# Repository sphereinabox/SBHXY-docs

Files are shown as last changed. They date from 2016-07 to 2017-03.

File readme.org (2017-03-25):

* SBHXY
SBHXY is an open source 3d Printer design using the [[http://corexy.com][Core XY]] motion system for XY, and is made in [[http://reprap.org][RepRap]] style except with a mix of printed and lasercut parts.

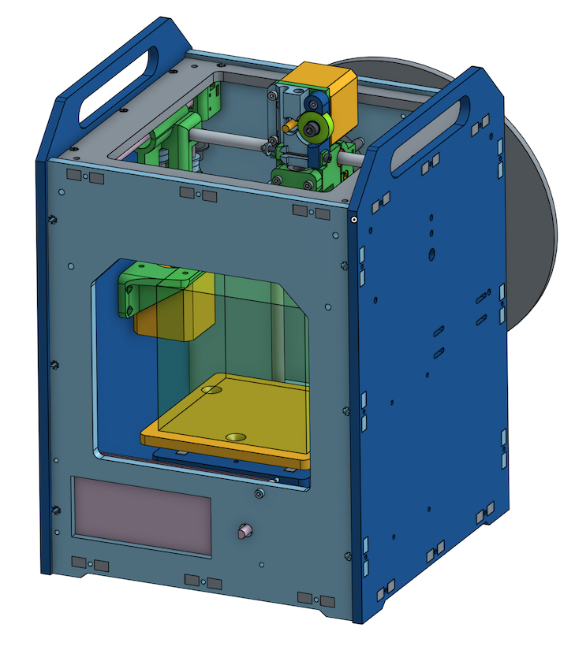
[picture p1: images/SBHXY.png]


SBHXY is licensed GPL v3.

SBHXY was designed to fit a small print volume in a relatively small amount of desk space. The print volume is 100x100x100mm, but the exterior dimensions, without print spool or top wires is only 227x220x316mm.

SBHXY was prototyped at the [[http://sbhackerspace.com][Santa Barbara Hackerspace]].

* TODO:
 - Add section to readme about getting started building this thing before getting to build manual
 - Make licensing + copyright notes in OnShape document
 - Link to OnShape document
 - DXFs are for the black or white Melamine which is 6.7mm thick?
 - Printrboard LCD PCB

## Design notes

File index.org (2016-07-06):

The assembly manual for the SBHXY: [[./build-manual.html]]

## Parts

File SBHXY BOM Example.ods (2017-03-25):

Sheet: BOM by Assembly
Qty | Part | Subassembly | Notes
2 | Printed Top Corner for Idler | Top Belt Idler
10 | M4 Hex Nut | Top Belt Idler
8 | M4x14 SHCS | Top Belt Idler | Only 4 really required. The top plate 2, and the lower printed part 2.
2 | M4x40 SHCS | Top Belt Idler
8 | 624 bearing for belt idler | Top Belt Idler
6 | M4 Flat Washer | Top Belt Idler | Go between pairs of bearings, and between bearings and printed parts
2 | Printed Bottom Corner for Idler | Top Belt Idler
2 | Printed Top Corner for Pulley (has bearing indent) | Top Belt Pulley End
2 | 625 Bearing 5x16x5 | Top Belt Pulley End
1 | Printed pulley spacer (shorter) | Top Belt Pulley End
1 | Printed pulley spacer (longer) | Top Belt Pulley End
2 | GT-2 Pulley 20 teeth 5mm bore | Top Belt Pulley End
2 | 5mm shaft, 100mm long | Top Belt Pulley End
6 | M4 Hex Nut | Top Belt Pulley End
6 | M4x14 SHCS | Top Belt Pulley End | Only top 2 required. Others may misalign rails
2 | 8mm hardened smooth rod, 173mm length | Top Belt Pulley End | Length must be within 1mm for lasercut frame length to fight tightly. Typically Y travel + 50 + 20 + homing margin
1 | Homing Switch SS-5GL | Top Belt Pulley End | S5GL size
2 | #4-1/2" wood screw | Top Belt Pulley End | Screws into printed plastic part
4 | M4 Hex Nut | Back Belt Pulley End
4 | M4x14 SHCS | Back Belt Pulley End
2 | 625 Bearing 5x16x5 | Back Belt Pulley End
2 | GT-2 Pulley 20 teeth 5mm bore | Back Belt Pulley End
2 | Stepper Motor 40mm long | AB Motors
2 | GT-2 Pulley 20 teeth 5mm bore | AB Motors
2.5 | GT-2 Belt length in meters | AB Motors | Should be 1 length over 2300mm long, or two lengths over 1200mm
8 | M3x10 SHCS | AB Motors
8 | M3 Flat Washer | AB Motors
8 | M3x12 SHCS | AB Motors
8 | M3 Flat Washer | AB Motors
8 | M3 Nylon Lock Nut | AB Motors | Hex nuts work but I found they get loose
2 | 140mm GT2 closed loop belt | AB Motors
1 | Printed Left X end | X Ends
1 | Printed Right X end | X Ends
4 | Printed X End Bearing Spacer | X Ends
8 | 624 bearing for belt idler | X Ends
4 | M4x45 SHCS | X Ends
4 | M4 Hex Nut | X Ends
4 | M4 Flat Washer | X Ends | Goes between bearings and printed x-end
2 | LM8LUU Linear Bearing 8x15x45 | X Ends
2 | 8mm hardened smooth rod, 173mm length | X Ends
1 | Printed Extruder Back Half | X Carriage Back Half
4 | LM8SUU Linear Bearing 8x15x17 | X Carriage Back Half
1 | Homing Switch - Small D2F-01L-D3 | X Carriage Back Half | This is smaller than the other homing switches
1 | #4-1/2" Wood screw | X Carriage Back Half
1 | 5015 12V Blower | X Carriage Back Half
2 | M3x20 FHCS | X Carriage Back Half | Phillips or hex is your choice . M3x20 SHCS may work but may rub in back of machine.
4 | M3 Hex Nut | X Carriage Back Half | Nut trap for blower duct, and blower
3 | M3 Hex Nut | X Carriage Back Half | Nut Traps for front half
2 | M3x35 SHCS | X Carriage Back Half | Belt tension adjustment screws
2 | M3 Hex Nut | X Carriage Adjustable Belt Clamp
1 | Printed Extruder Belt Clamp | X Carriage Adjustable Belt Clamp | The belt presses into a slot
1 | Printed Extruder Belt Clamp Mirror | X Carriage Adjustable Belt Clamp
2 | M3x35 SHCS | X Carriage Adjustable Belt Clamp
1 | Printed X Fixed belt clamp (ribbed plate with single hole) | X Carriage Fixed Belt Clamp
1 | M3x16 SHCS | X Carriage Fixed Belt Clamp
1 | Printed X carriage front half | X Carriage Front Half
3 | M3x25 SHCS | X Carriage Front Half | These hold front/back together
2 | M3 Hex Nut | X Carriage Front Half | Nut trap for hotend clamp
1 | Stepper Motor 40mm long | X Carriage Front Half | Extruder motor
1 | M3x10 FHCS | X Carriage Front Half | Phillips or socket is your choice. The material is not thick enough for a standard socket head screw
1 | Filament Drive Gear (6mm hobb diameter) | X Carriage Front Half
3 | 4 inch nylon zip tie | X Carriage Front Half | Mount to linear bearings
1 | Printed Hotend Clamp | X Carriage Front Half | Hold thermistor in place
2 | M3 Hex Nut | X Carriage Front Half | Nut trap for hotend clamp
1 | Printed Extruder Blower Duct | X Carriage Duct
2 | M3x10 SHCS | X Carriage Duct
1 | Printed Hotend Clamp | Hotend Clamp
2 | M3x20 SHCS | Hotend Clamp
1 | Printed Extruder Plate | Extruder Plate
2 | M3x12 SHCS | Extruder Plate
2 | 4 inch nylon zip tie | Extruder Plate
1 | Large filament Guide Tube (approx 1/4" OD) maybe 18" long max | Extruder Plate
1 | Printed Extruder Idler Lever Arm | Extruder Lever Arm
1 | M3x16 SHCS | Extruder Lever Arm | Pivot
1 | 608 Bearing | Extruder Lever Arm | Filament idler bearing
1 | M5x10 SHCS | Extruder Lever Arm | Screws into printed part, holds idler bearing in place
1 | M5 Flat Washer | Extruder Lever Arm
1 | M3x45 SHCS | Extruder Tension Adjustment Bolt
2 | Printed Extruder Idler Pivot | Extruder Tension Adjustment Bolt
2 | M4 Flat Washer | Extruder Tension Adjustment Bolt | Large enough to keep spring on bolt
1 | Extruder Spring | Extruder Tension Adjustment Bolt
1 | M3 Hex Nut | Extruder Tension Adjustment Bolt
1 | E3d V6 Lite | Hotend Assembly | Includes thermistor, heater cartridge, 30mm fan, duct for fins, and PTFE tubing sticking out about 3 inches of groove mount.
1 | Printed Z Idler | Z Top Rod Holder
2 | M3 Hex Nut | Z Top Rod Holder
2 | M3x12 SHCS | Z Top Rod Holder | Through back plane
2 | 624 bearing for belt idler | Z Top Rod Holder
2 | M4 Flat Washer | Z Top Rod Holder
1 | M4 Hex Nut | Z Top Rod Holder
1 | M4x20 SHCS | Z Top Rod Holder
1 | Printed Z motor Mount | Z Bottom Rod Holder
2 | 8mm hardened smooth rod, 173mm length | Z Bottom Rod Holder
1 | Stepper Motor 40mm long | Z Bottom Rod Holder
4 | M3x10 SHCS | Z Bottom Rod Holder
1 | GT-2 Pulley 20 teeth 5mm bore | Z Bottom Rod Holder
6 | M3 Hex Nut | Z Bottom Rod Holder
6 | M3x12 SHCS | Z Bottom Rod Holder | 4 through bottom, 2 through back of frame
1 | Printed Z homing switch mount | Z Homing Switch Mount
1 | Homing Switch SS-5GL | Z Homing Switch Mount
2 | #4-1/2" Wood Screw | Z Homing Switch Mount
2 | M3 Hex Nut | Z Homing Switch Mount
2 | M3x25 SHCS | Z Homing Switch Mount
1 | Lasercut Z Carriage Back | Z Carriage
2 | Lasercut Z Carriage Side | Z Carriage
1 | Lasercut Z Carriage Top | Z Carriage | This has slots to fit into the side pieces
1 | Lasercut Print Bed | Z Carriage | This has 3 holes. They need to be drilled countersunk
4 | Printed Z Bearing Holder | Z Carriage
1 | Printed Z Belt Holder | Z Carriage
2 | LM8LUU Linear Bearing 8x15x45 | Z Carriage | 4 of LM8UU is fine
8 | M3 Hex Nut | Z Carriage | Inside nut traps on printed parts
6 | M3x12 SHCS | Z Carriage | Go into printed parts
2 | M3x16 SHCS | Z Carriage | Z Homging Switch Adjustment mount
3 | M3x30 FHCS | Z Carriage | Bed-level adjustment
4 | M3 Hex Nut | Z Carriage | Captive in side lasercut pieces
4 | M3x12 SHCS | Z Carriage | Through Z top plate into side lasercut pieces
3 | Extruder Spring | Z Carriage | Bed-level adjustment
3 | Printed Thumb Nut Adapter | Z Carriage | Bed-level adjustment
6 | M3 Hex Nut | Z Carriage | Bed level adjustment, and holding bed screws in place
1 | Painters Tape, approx 5 inches square | Z Carriage | Print surface
0.4 | GT-2 Belt length in meters | Z Carriage
1 | Printed Z Homing Switch Adjust | Z Carriage Homing Adjust
1 | M3x20 SHCS | Z Carriage Homing Adjust
1 | Extruder Spring | Z Carriage Homing Adjust
1 | M3 Hex Nut | Z Carriage Homing Adjust
2 | M4 Flat Washer | Z Carriage Homing Adjust
1 | Lasercut top plate | Top Plate
12 | M3 Hex Nut | Top Plate | Nut Traps
1 | Lasercut back plate | Back Plate
6 | M3 Hex Nut | Back Plate | Nut Traps
6 | M3x12 SHCS | Back Plate | Into other panel nut traps
1 | Printed Spool Holder | Back Plate
1 | Printed Power Jack Mount | Power Jack Mount
1 | Panel Mount Barrel Jack Cable | Power Jack Mount
2 | M3 Hex Nut | Power Jack Mount
2 | M3x12 SHCS | Power Jack Mount
1 | Printed Filament Guide Mount | Filament Guide Mount
2 | 4 inch nylon zip tie | Filament Guide Mount
2 | M3 Hex Nut | Filament Guide Mount
2 | M3x12 SHCS | Filament Guide Mount
1 | Lasercut Left Plate | Left Plate
12 | M3x12 SHCS | Left Plate | Into other panel nut traps
1 | Lasercut Right Plate | Right Plate
12 | M3x12 SHCS | Right Plate | Into other panel nut traps
1 | Printrboard electronics | Right Plate
4 | Electronics Spacers 2mm tall | Right Plate | Printrboard mounting
4 | M3 Nylon Lock Nut | Right Plate | Printrboard mounting
4 | M3x20 SHCS | Right Plate | Printrboard mounting
1 | Lasercut Bottom Plate | Bottom Plate | Into ends of extrusion
12 | M3 Hex Nut | Bottom Plate | Nut Traps
4 | Adhesive rubber foot | Bottom Plate | Must be over 8mm tall. The foot should be adhesive to the bottom plate not to the thin laser edge
1 | Lasercut Front Plate | Front Plate
6 | M3 Hex Nut | Front Plate | Nut Traps
6 | M3x12 SHCS | Front Plate | Into other panel nut traps
1 | RepRapDiscount Smart Controller (20x4 Text) | Front Plate | LCD Mounting
4 | M3 Nylon Lock Nut | Front Plate | LCD Mounting
4 | Printed LCD Spacer (10mm) | Front Plate | LCD Mounting
1 | Printed LCD Knob | Front Plate
4 | M3x25 SHCS | Front Plate | LCD Mounting
6 | M3 Hex Nut | Front Plate | Nut Traps
1 | Printrboard LCD+fans PCB | Printrboard add-on
2 | [mosfet] | Printrboard add-on
2 | [diode] | Printrboard add-on
? | [connectors?] | Printrboard add-on
1 | Allen Key Set | Tools
1 | Spool of PLA filament, 1.75mm diameter | Tools
1 | USB A to Micro B cable | Tools
1 | 12V 6A power supply | Electronics

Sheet: BOM by Part
Part Name | Qty Required | Source | Price | Qty | Notes
Lasercut Top Plate | 1
Lasercut Bottom Plate | 1
Lasercut Back Plate | 1
Lasercut Front Plate | 1
Lasercut Left Plate | 1
Lasercut Right Plate | 1
Lasercut Z Carriage Back | 1
Lasercut Z Carriage Side | 2
Lasercut Z Carriage Top | 1
Lasercut Print Bed | 1
Printed Top Corner for Idler | 2
Printed Bottom Corner for Idler | 2
Printed Top Corner for Pulley (has bearing indent) | 2
Printed pulley spacer (shorter) | 1
Printed pulley spacer (longer) | 1
Printed Left X end | 1
Printed Right X end | 1
Printed X End Bearing Spacer | 1
Printed Extruder Back Half | 1
Printed Extruder Belt Clamp | 1
Printed Extruder Belt Clamp Mirror | 1
Printed X Fixed belt clamp (ribbed plate with single hole) | 1
Printed X carriage front half | 1
Printed Hotend Clamp | 2
Printed Extruder Blower Duct | 1
Printed Extruder Plate | 1
Printed Extruder Idler Lever Arm | 1
Printed Extruder Idler Pivot | 2
Printed Z Idler | 1
Printed Z motor Mount | 1
Printed Z homing switch mount | 1
Printed Z Bearing Holder | 4
Printed Z Belt Holder | 1
Printed Thumb Nut Adapter | 3
Printed Z Homing Switch Adjust | 1
Printed Power Jack Mount | 1
Printed Filament Guide Mount | 1
Printed Spool Holder | 1
Printed LCD Spacer (10mm) | 4
Printed LCD Knob | 1
Filament Drive Gear (6mm hobb diameter) | 1 | http://www.robotdigg.com/product/242/MK8-Filament-Drive-Gear | $3.00 | 1
Homing Switch SS-5GL | 2 | http://www.robotdigg.com/product/141/Endstop,-Snap-Action-Limit-Switch-SS-5GL | $0.60 | 1 | No wires
Homing Switch - Small D2F-01L-D3 | 1 | http://www.digikey.com/product-detail/en/D2F01LD3/Z5203-ND/1811799 | $20.50 | 10 | -D3 is for soldering leads on. Without extension is intended for PCB and is .25 to .50 cheaper
Stepper Motor 40mm long | 4 | http://www.robotdigg.com/product/7/NEMA17-Stepper-Motor-40mm-Long,-1.2A | $6.80 | 1
608 Bearing | 1 | http://www.robotdigg.com/product/12/608ZZ-Ball-Bearing | $0.30 | 1
625 Bearing 5x16x5 | 4 | http://www.robotdigg.com/product/63/625ZZ+Ball+Bearing | $4.00 | 10
GT-2 Belt length in meters | 2.9 | http://www.robotdigg.com/product/10/Open-Ended-6mm-Width-GT2-Belt | $1.80 | 1 | Sold by meter
140mm GT2 closed loop belt | 2 | http://www.robotdigg.com/product/88/140mm,+150mm+OR+154mm+2GT-6+endless+belt | $0.35 | 1
LM8LUU Linear Bearing 8x15x45 | 4 | http://www.robotdigg.com/product/302/LM8LUU+8*15*45+Linear+Bearing | $1.00 | 1
LM8SUU Linear Bearing 8x15x17 | 4 | http://www.robotdigg.com/product/477/LMS8UU+Short+Linear+Bearing | $0.60 | 1
GT-2 Pulley 20 teeth 5mm bore | 7 | http://www.robotdigg.com/product/9/GT2-Pulley-20-Teeth-5mm-Bore | $1.80 | 1
5015 12V Blower | 1 | http://www.robotdigg.com/product/194/5015+12V+Blow+Fan | $1.40 | 1 | 0.1A version
E3d V6 Lite | 1 | http://www.filastruder.com/products/lite6 | $35.00 | 1 | 1.75mm 12V Direct version still comes with enough bowden tube
Printrboard electronics | 1
Printrboard to barrel jack adapter cable | 0
12V 6A power supply | 1
RepRapDiscount Smart Controller (20x4 Text) | 1 | http://www.robotdigg.com/product/122/RAMPS+LCD2004+with+SD+Socket | $10.80 | 1 | Poor assembly quality and encoder
8mm hardened smooth rod, 173mm length | 6 | Misumi PSFJ8-173 | $6.70 | 1 | Hard chromed
5mm shaft, 100mm long | 2 | http://www.amazon.com/Helicopter-100mm-Ground-Shaft-Round/dp/B00NQ9NBWQ/ | $9.00 | 10
Extruder Spring | 5 | http://www.mcmaster.com/nav/enter.asp?partnum=9657K274 | $9.80 | 12
Allen Key Set | 1 | http://www.robotdigg.com/product/128/1.5,-2,-2.5,-3,-4-size-allen-key-with-ball-head-in-pack | $2.00 | 1
4 inch nylon zip tie | 7 | http://www.robotdigg.com/product/127/Nylon-Cable-Ties-2.5*100mm-100pcs-n-3.6*200mm-100pcs-Pack | $1.80 | 100 | Probably should specify 2.5 or 3.6mm width when ordering
USB A to Micro B cable | 1 | http://www.monoprice.com/Product?c_id=103&cp_id=10303&cs_id=1030307&p_id=4867&seq=1&format=2 | $0.74 | 1
Spool of PLA filament, 1.75mm diameter | 1 |  | $30.00 | 1
M2.5x5 SHCS | 0 | https://www.boltdepot.com/Product-Details.aspx?product=6369 | $6.13 | 100
M2.5x6 SHCS | 0 | https://www.boltdepot.com/Product-Details.aspx?product=6370 | $6.44 | 100
M2.5x8 SHCS | 0 | https://www.boltdepot.com/Product-Details.aspx?product=6371 | $6.50 | 100
M2.5x10 SHCS | 0 | https://www.boltdepot.com/Product-Details.aspx?product=6372 | $7.28 | 100
M2.5x12 SHCS | 0 | https://www.boltdepot.com/Product-Details.aspx?product=6373 | $9.09 | 100
M2.5x16 SHCS | 0 | https://www.boltdepot.com/Product-Details.aspx?product=6374 | $10.53 | 100
M2.5x20 SHCS | 0 | https://www.boltdepot.com/Product-Details.aspx?product=6375 | $11.70 | 100
M2.5 Flat Washer | 0 | https://www.boltdepot.com/Product-Details.aspx?Units=Metric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 | $1.05 | 100
M2.5 Hext Nut | 0 | https://www.boltdepot.com/Product-Details.aspx?Units=Metric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 | $1.75 | 100
M3x8 SHCS | 0 | https://www.boltdepot.com/Product-Details.aspx?product=6379 | $3.60 | 100
M3x10 SHCS | 14 | https://www.boltdepot.com/Product-Details.aspx?product=6380 | $3.78 | 100
M3x12 SHCS | 68 | https://www.boltdepot.com/Product-Details.aspx?product=6381 | $3.92 | 100
M3x16 SHCS | 4 | https://www.boltdepot.com/Product-Details.aspx?product=6382 | $3.97 | 100
M3x20 SHCS | 7 | https://www.boltdepot.com/Product-Details.aspx?product=6383 | $4.28 | 100
M3x25 SHCS | 9 | https://www.boltdepot.com/Product-Details.aspx?product=6384 | $5.16 | 100
M3x30 SHCS | 0 | https://www.boltdepot.com/Product-Details.aspx?product=6385 | $6.09 | 100
M3x35 SHCS | 4 | https://www.boltdepot.com/Product-Details.aspx?product=6386 | $9.29 | 100
M3x40 SHCS | 0 | https://www.boltdepot.com/Product-Details.aspx?product=6387 | $9.73 | 100
M3x45 SHCS | 1 | https://www.boltdepot.com/Product-Details.aspx?product=6388 | $10.84 | 100
M3x20 Flat Head | 0 | https://www.boltdepot.com/Product-Details.aspx?product=6869 | $5.55 | 100
M3x25 Flat Head | 0 | https://www.boltdepot.com/Product-Details.aspx?product=6870 | $7.10 | 100
M3 Flat Washer | 16 | https://www.boltdepot.com/Product-Details.aspx?product=4513 | $1.10 | 100
M3 Hex Nut | 89 | https://www.boltdepot.com/Product-Details.aspx?product=4773 | $1.80 | 100
M3 Nylon Lock Nut | 16 | https://www.boltdepot.com/Product-Details.aspx?product=4792 | $3.19 | 100
M3 Lock Washer | 0 | https://www.boltdepot.com/Product-Details.aspx?product=14836 | $1.90 | 100
M4x10 SHCS | 0 | https://www.boltdepot.com/Product-Details.aspx?product=6393 | $4.92 | 100
M4x12 SHCS | 0 | https://www.boltdepot.com/Product-Details.aspx?product=6394 | $5.42 | 100
M4x14 SHCS | 18 | https://www.boltdepot.com/Product-Details.aspx?product=6395 | $5.78 | 100
M4x16 SHCS | 0 | https://www.boltdepot.com/Product-Details.aspx?product=6396 | $6.01 | 100
M4x18 SHCS | 0 | https://www.boltdepot.com/Product-Details.aspx?product=6397 | $8.66 | 100
M4x20 SHCS | 1 | https://www.boltdepot.com/Product-Details.aspx?product=6398 | $7.21 | 100
M4x25 SHCS | 0 | https://www.boltdepot.com/Product-Details.aspx?product=6399 | $7.78 | 100
M4x30 SHCS | 0 | https://www.boltdepot.com/Product-Details.aspx?product=6400 | $9.57 | 100
M4x35 SHCS | 0 | https://www.boltdepot.com/Product-Details.aspx?product=6401 | $11.52 | 100
M4x40 SHCS | 2 | https://www.boltdepot.com/Product-Details.aspx?product=6402 | $12.73 | 100
M4x45 SHCS | 4 | https://www.boltdepot.com/Product-Details.aspx?product=6403 | $15.45 | 100
M4x50 SHCS | 0 | https://www.boltdepot.com/Product-Details.aspx?product=6404 | $18.84 | 100
M4 Flat Washer | 16 | https://www.boltdepot.com/Product-Details.aspx?product=4514 | $1.25 | 100
M4 Hex Nut | 25 | https://www.boltdepot.com/Product-Details.aspx?product=4774 | $2.09 | 100
M4 Nylon Lock Nut | 0 | https://www.boltdepot.com/Product-Details.aspx?product=4793 | $3.60 | 100
M4 Lock Washer | 0 | https://www.boltdepot.com/Product-Details.aspx?product=14837 | $2.06 | 100
M5x8 SHCS | 0 | https://www.boltdepot.com/Product-Details.aspx?product=6406 | $7.21 | 100
M5x10 SHCS | 1 | https://www.boltdepot.com/Product-Details.aspx?product=6407 | $7.45 | 100
M5x12 SHCS | 0 | https://www.boltdepot.com/Product-Details.aspx?product=6408 | $7.60 | 100
M5x16 SHCS | 0 | https://www.boltdepot.com/Product-Details.aspx?product=6409 | $9.26 | 100
M5x20 SHCS | 0 | https://www.boltdepot.com/Product-Details.aspx?product=6410 | $10.58 | 100
M5x25 SHCS | 0 | https://www.boltdepot.com/Product-Details.aspx?product=6411 | $11.32 | 100
M5x30 SHCS | 0 | https://www.boltdepot.com/Product-Details.aspx?product=6412 | $14.27 | 100
M5x35 SHCS | 0 | https://www.boltdepot.com/Product-Details.aspx?product=6413 | $18.01 | 100
M5x40 SHCS | 0 | https://www.boltdepot.com/Product-Details.aspx?product=6414 | $21.26 | 100
M5x45 SHCS | 0 | https://www.boltdepot.com/Product-Details.aspx?product=6452 | $22.29 | 100
M5x50 SHCS | 0 | https://www.boltdepot.com/Product-Details.aspx?product=6453 | $28.15 | 100
M5 Flat Washer | 1 | https://www.boltdepot.com/Product-Details.aspx?Units=Metric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 | $1.75 | 100
M5 Hex Nut | 0 | https://www.boltdepot.com/Product-Details.aspx?Units=Metric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 | $2.79 | 100
M5 Nylon Lock Nut | 0 | https://www.boltdepot.com/Product-Details.aspx?product=4794 | $4.19 | 100
M5 Lock Washer | 0 | https://www.boltdepot.com/Product-Details.aspx?Units=Metric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 | $2.56 | 100
M5x8 BHCS | 0 | https://www.boltdepot.com/Product-Details.aspx?product=6631 | $5.87 | 100
M5x10 BHCS | 0 | https://www.boltdepot.com/Product-Details.aspx?product=6632 | $6.07 | 100
M5x12 BHCS | 0 | https://www.boltdepot.com/Product-Details.aspx?product=6633 | $6.50 | 100
M5x16 BHCS | 0 | https://www.boltdepot.com/Product-Details.aspx?product=6634 | $7.26 | 100
M5x20 BHCS | 0 | https://www.boltdepot.com/Product-Details.aspx?product=6635 | $8.85 | 100
M5x25 BHCS | 0 | https://www.boltdepot.com/Product-Details.aspx?product=6636 | $10.61 | 100
M5x30 BHCS | 0 | https://www.boltdepot.com/Product-Details.aspx?product=6637 | $13.15 | 100
#4-1/2" Wood screw | 5 | https://www.boltdepot.com/Product-Details.aspx?product=2470 | $1.34 | 100
M3x10 FHCS | 1 | https://www.boltdepot.com/Product-Details.aspx?product=13251 | $7.07 | 100
M3x20 FHCS | 2 | https://www.boltdepot.com/Product-Details.aspx?product=13254 | $9.50 | 100
M3x30 FHCS | 3 | https://www.boltdepot.com/Product-Details.aspx?product=13256 | $12.59 | 100

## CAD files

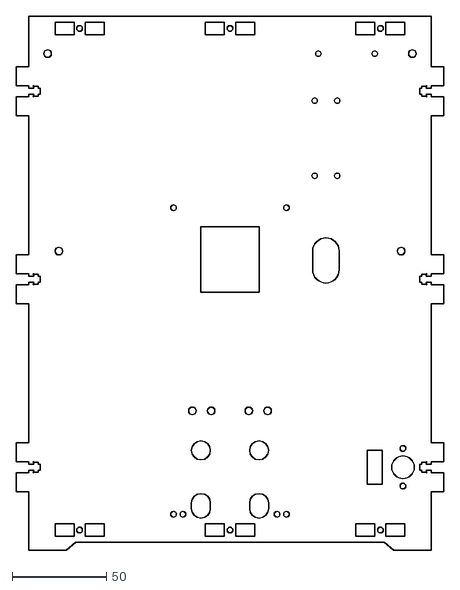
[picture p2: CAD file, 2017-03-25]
DXF/Lasercut Frame - Face-5.dxf
227.6 x 284.0

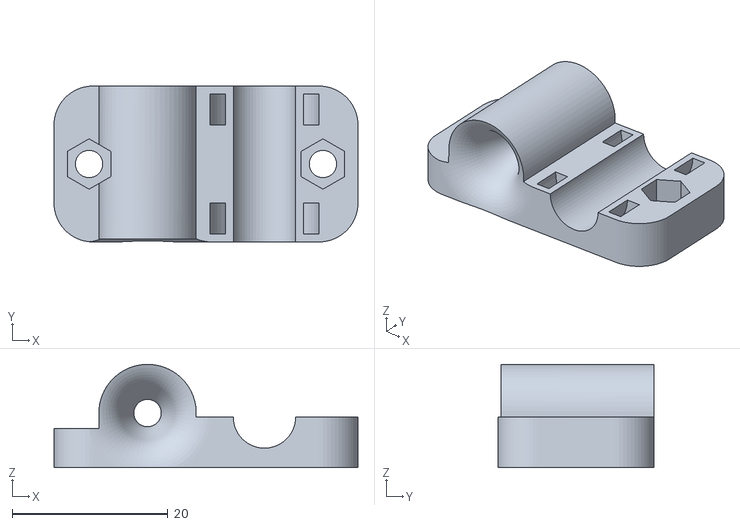
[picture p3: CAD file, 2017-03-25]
STL/Small CoreXY 2 - Filament Tube Mount.stl
39.0 x 20.0 x 13.2

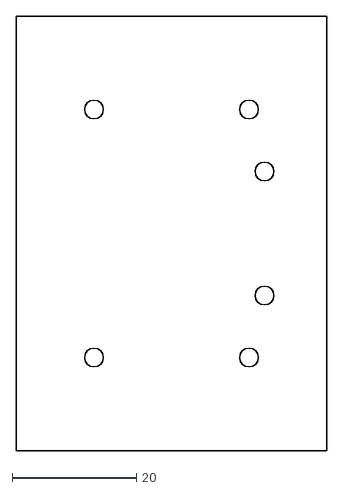
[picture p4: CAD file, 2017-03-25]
DXF/Z Lasercut Parts - Face-2.dxf
50.0 x 70.0

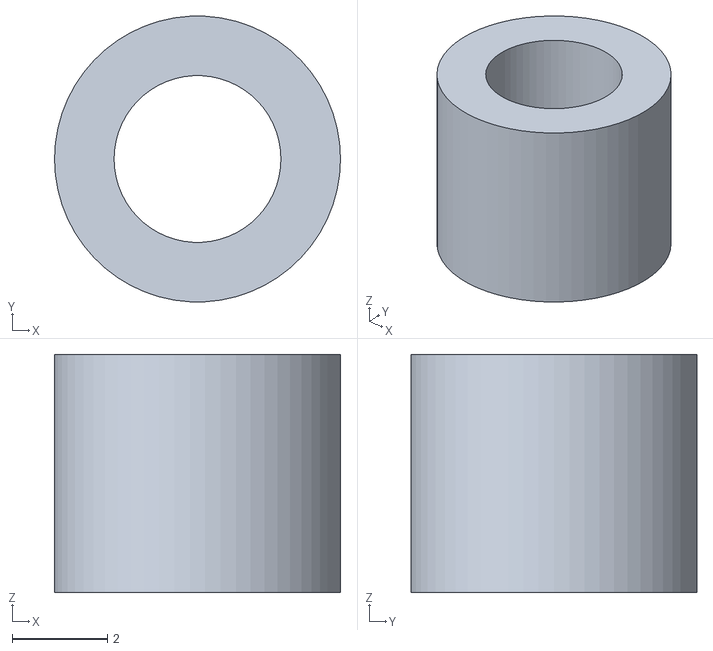
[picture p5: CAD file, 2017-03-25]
STL/Small CoreXY 2 - Printrboard Spacer.stl
6.00 x 5.99 x 5.00

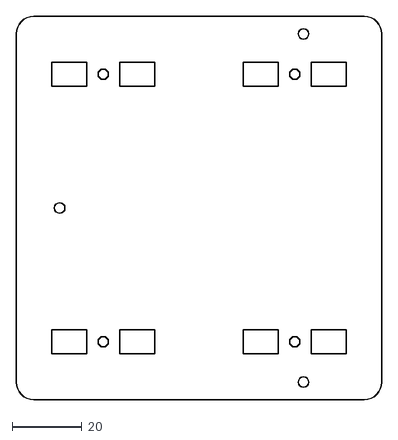
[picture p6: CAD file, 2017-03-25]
DXF/Z Lasercut Parts - Face-3.dxf
105.0 x 110.0

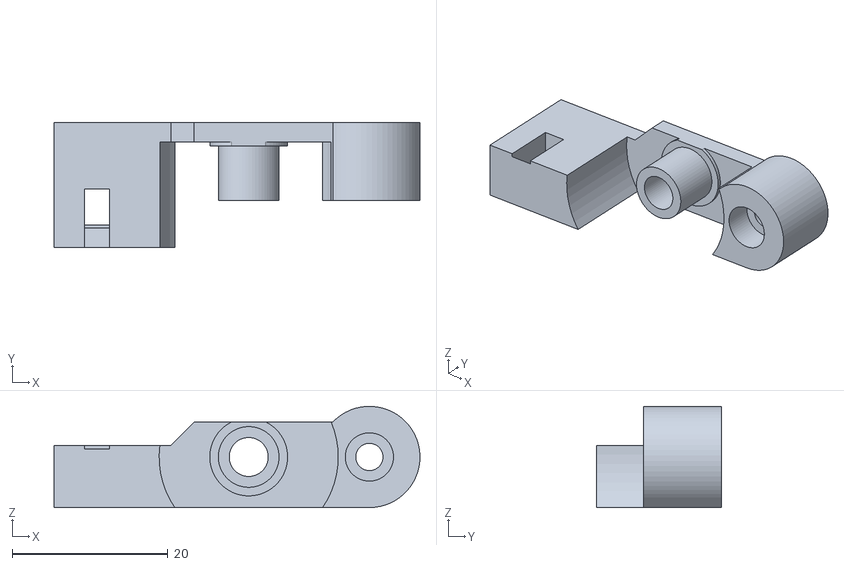
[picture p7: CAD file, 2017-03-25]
STL/Small CoreXY 2 - Extruder Idler Mount.stl
47.0 x 16.0 x 13.0

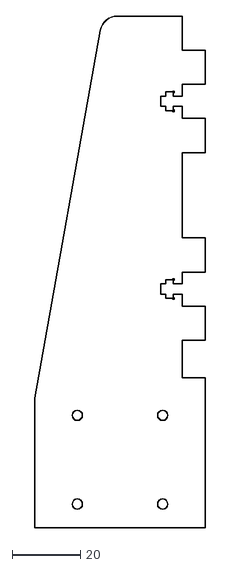
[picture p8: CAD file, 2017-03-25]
DXF/Z Lasercut Parts - Face.dxf
50.0 x 150.0

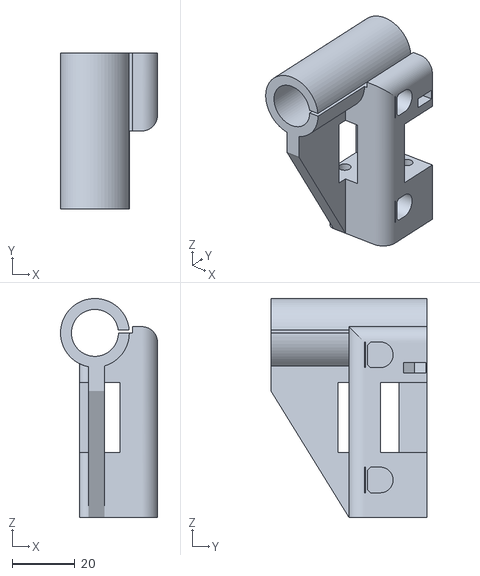
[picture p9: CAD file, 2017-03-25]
STL/Small CoreXY 2 - X End Idler.stl
31.0 x 50.0 x 70.0

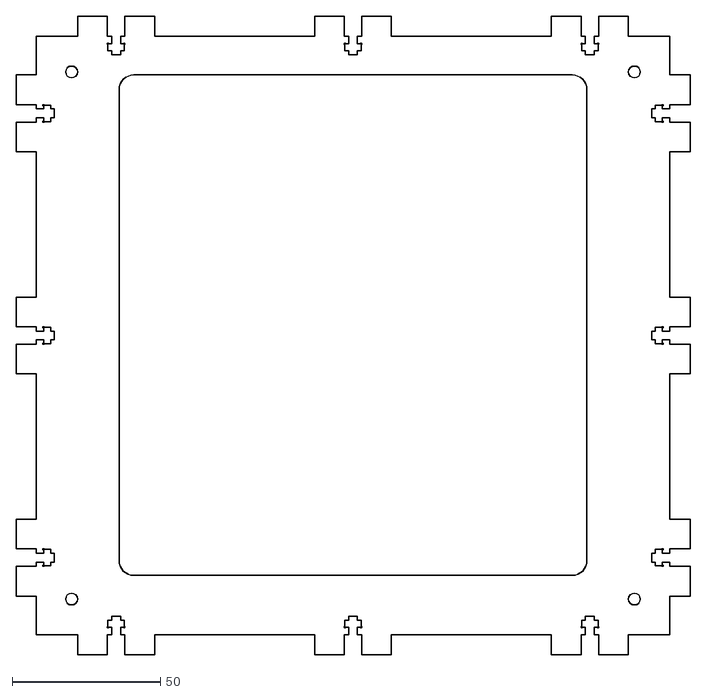
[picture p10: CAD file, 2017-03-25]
DXF/Lasercut Frame - Face-4.dxf
227.6 x 215.6

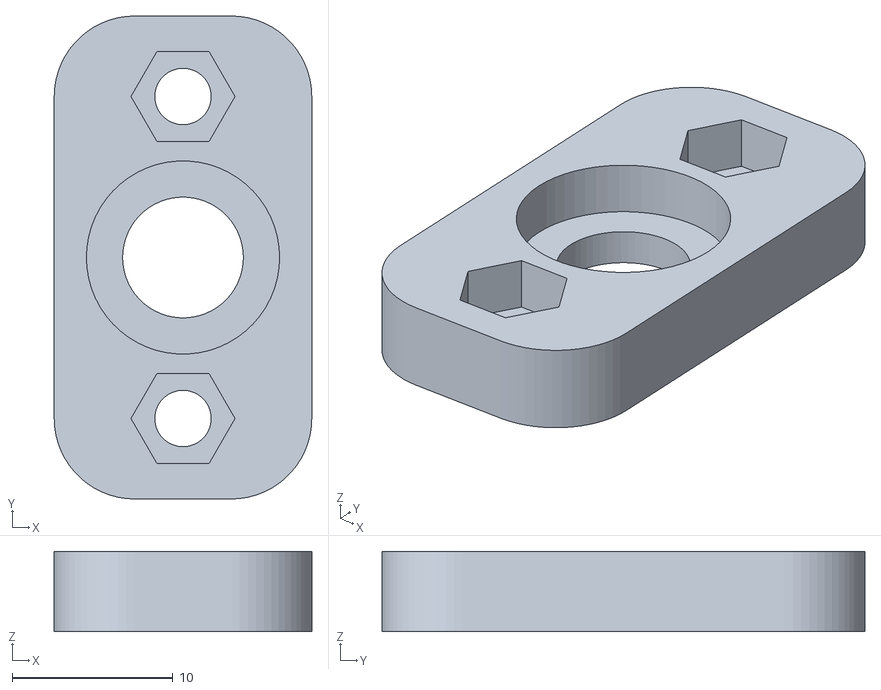
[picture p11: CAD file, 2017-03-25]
STL/Small CoreXY 2 - Barrel Jack Plate.stl
16.0 x 30.0 x 5.00

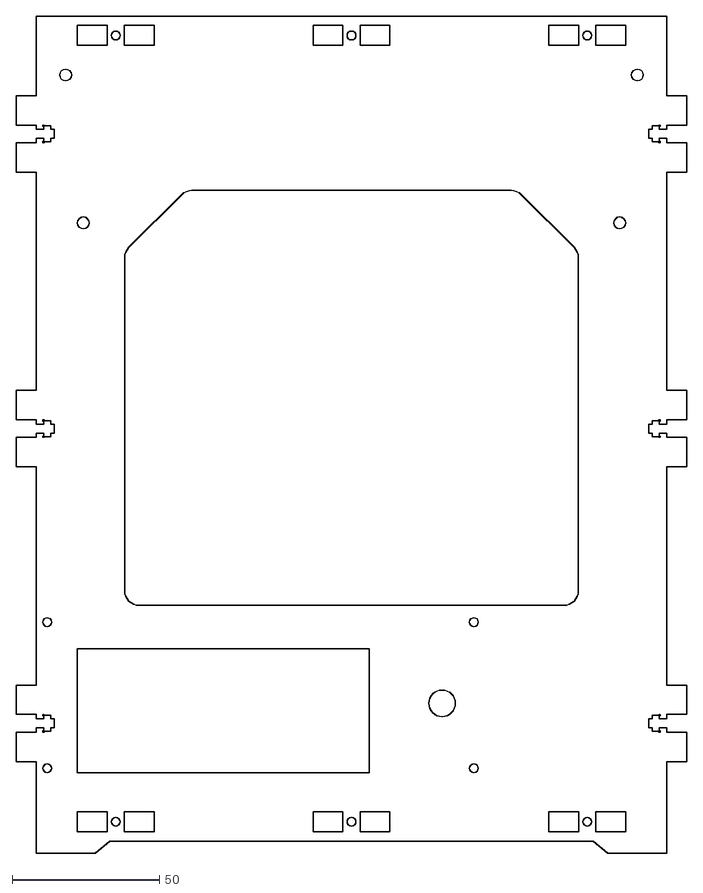
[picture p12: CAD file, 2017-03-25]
DXF/Lasercut Frame - Face-2.dxf
227.6 x 284.0

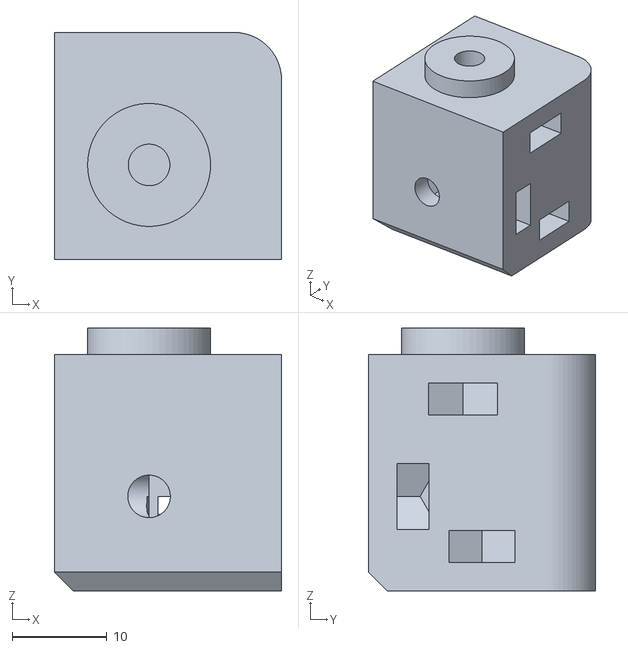
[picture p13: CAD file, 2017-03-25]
STL/Small CoreXY 2 - Top Corner Idler.stl
24.0 x 24.0 x 27.8

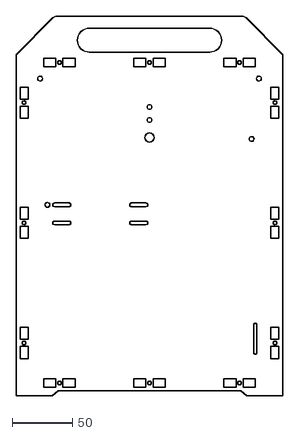
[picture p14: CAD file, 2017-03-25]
DXF/Lasercut Frame - Face-3.dxf
222.0 x 316.0

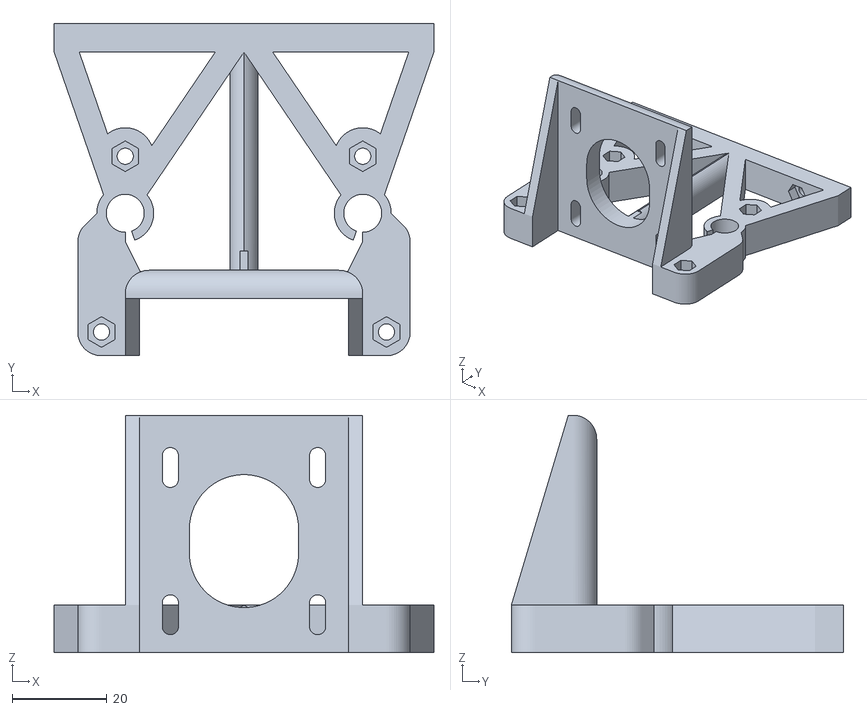
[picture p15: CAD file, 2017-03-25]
STL/Small CoreXY 2 - Z Motor Mount.stl
80.0 x 70.0 x 50.0

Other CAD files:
DXF/Z Lasercut Parts - Face-4.dxf
STL/Small CoreXY 2 - Z Idler.stl
DXF/Lasercut Frame - Face-6.dxf
DXF/Lasercut Frame - Face.dxf
STL/Blower Duct Mk3 - Blower Duct Mk3.stl
STL/Small CoreXY 2 - Bottom Corner 625.stl
STL/Small CoreXY 2 - Bottom Corner Idler.stl
STL/Small CoreXY 2 - Extruder Filament Plate.stl
STL/Small CoreXY 2 - Hotend Clamp.stl
STL/Small CoreXY 2 - Idler Spacer.stl
STL/Small CoreXY 2 - LCD Spacer.stl
STL/Small CoreXY 2 - Thumb Nut Adapter M3.stl
STL/Small CoreXY 2 - Top Corner 625 Mirror.stl
STL/Small CoreXY 2 - Top Corner 625.stl
STL/Small CoreXY 2 - Top Corner Idler Mirror.stl
STL/Small CoreXY 2 - X Belt Clamp Adjustable Mirror.stl
STL/Small CoreXY 2 - X Belt Clamp Adjustable.stl
STL/Small CoreXY 2 - X Belt Clamp Fixed.stl
STL/Small CoreXY 2 - X Carriage Back.stl
STL/Small CoreXY 2 - X Carriage Front.stl
STL/Small CoreXY 2 - X End Idler Mirror.stl
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

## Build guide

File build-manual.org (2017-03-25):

* SBHXY Build Manual

This is the build manual for the SBHXY.

* Common Build Hints

There are a couple of things that make easier.

** Captive Nuts

Captive nuts that go flat into a part are easier to insert using a longer bolt to push them in.

Captive nuts that go in sideways fit in with the point first into the
part and are easier to insert with pliers. Once you get it started use
the tips of your pliers to push the nut in the rest of the way.

** "Tightness"

[don't over tighten bolts. Most of the nuts on this printer sit in
printed parts or wood which will colapse or deform when over-tightened
which may prevent you from disassembling it later and will end up
looser than tightening the screws "just enough"]

[how do you know how much is enough?]

** [fitting laser slots together]

[these might be tight. If you hammer them or pull unevenly apart the melamine kind of delaminates.]

* Assembly Instructions

* Front Panel

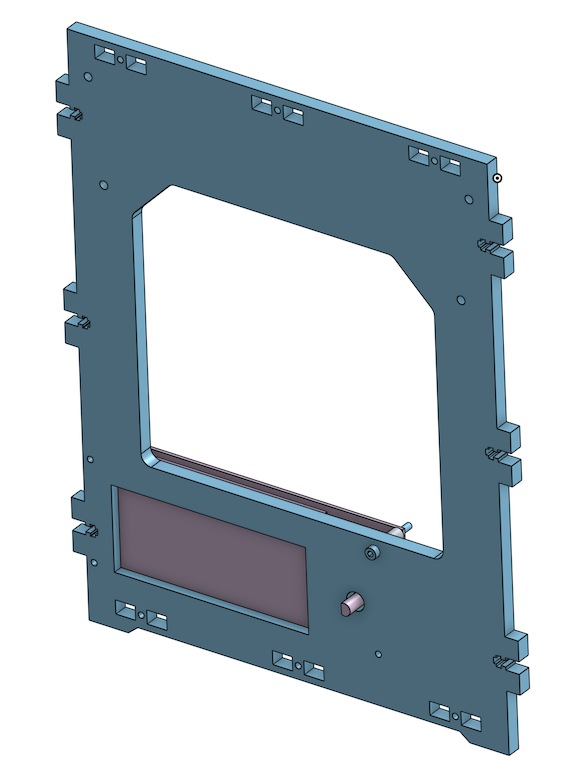
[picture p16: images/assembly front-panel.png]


Parts:
 * Lasercut front panel
 * 4 of M3x25 SHCS
 * 4 of 10mm spacer with 3mm hole
 * 4 of M3 nylon lock nut
 * RepRapDiscount Smart Controller or clone
 * Optional: foam or foam tape, approximately 3mm thick

If your LCD is loose from the back PCB of the LCD, it will vibrate and make noise. Put foam between the two.

Install the LCD with 10mm spacers and M3x25 and lock nuts. The LCD
will be on the lower left corner as viewed from the front of the
machine, with the SD card sticking out to the left and the knob on the
right of the LCD.

* Frame "Skeleton"

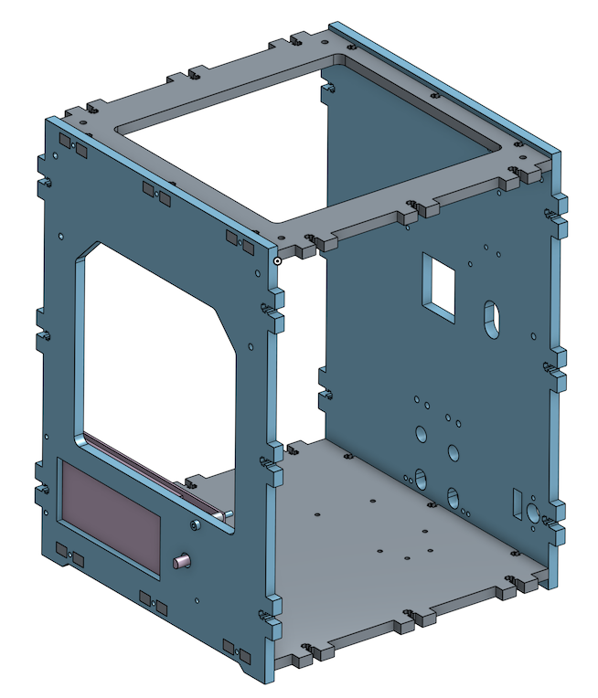
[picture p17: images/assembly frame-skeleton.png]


Parts:
 * Lasercut front panel (with LCD installed)
 * Lasercut bottom panel
 * Lasercut back panel
 * Lasercut top panel
 * 12 of M3 hex nut
 * 12 of M3x12 SHCS

Assemble the following frame pieces: Top, Front, Bottom, Back. M3 nuts
are inserted into the traps then M3x12 bolts go through front and back
panels to hold the pieces together.

The bottom panel has the holes towards the back of the machine, with
the pair of non-symetrical holes on the right as the assembled machine
is viewed from the front. These holes mount the Z homing switch.

The back panel has a slot near the top corner, this also goes towards
the right as viewed from the front of the assembled machine.

The top panel is the same in every direction.

* Z-Axis

** Z Motor mount

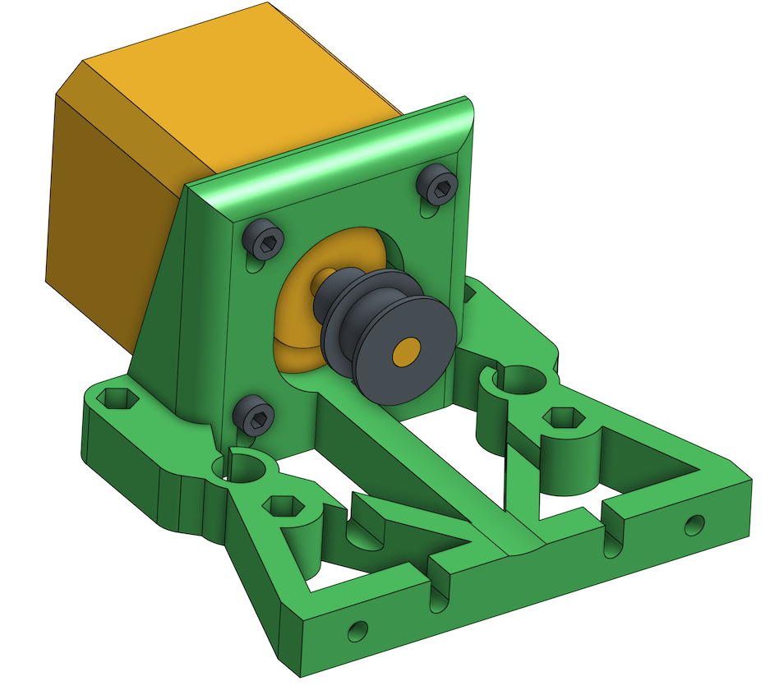
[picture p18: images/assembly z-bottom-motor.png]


Parts:
 * Printed Z motor mount
 * 6 of M3 hex nuts
 * 4 of M3x10 SHCS
 * NEMA17 Stepper Motor
 * GT2 Belt Pulley, 20 teeth with setscrews

Install the 6 M3 hex nuts into the traps using longer M3 bolts. The
ones going through the side of the printed part are easier to install
by putting the long bolt through, then threading the nut on, then
pulling bolt to seat the nut, then unscrewing the bolt.

** Z Idler

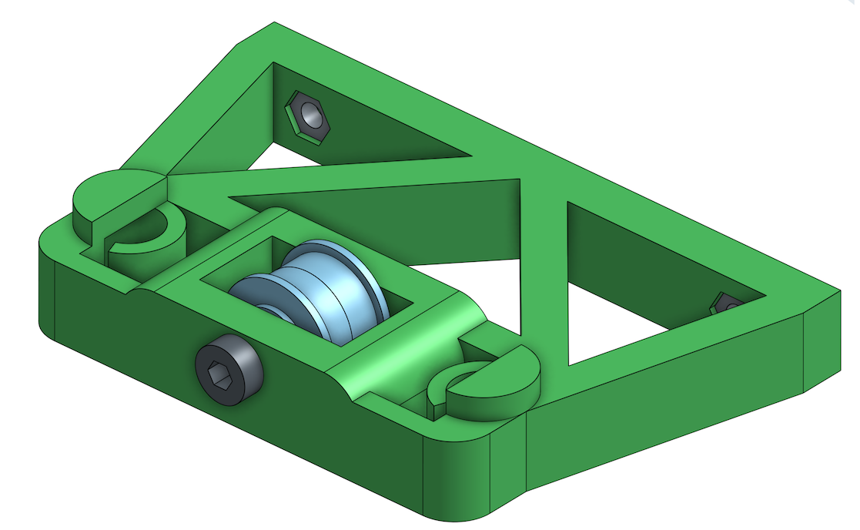
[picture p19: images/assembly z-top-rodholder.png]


Parts:
 * Printed Z idler mount
 * 2 of 624 Flanged bearings
 * M4x20 SHCS
 * M4 hex nut
 * 2 of M4 flat Washer

Insert the washers on the outside, bearing pair in the middle into the
hole for the belt idler, insert the nut and bolt. The bearings should
spin easily, and not be loose between the printed part to slide along the bolt.

Insert the two M3 nuts into the nut traps using longer bolts to pull
them in place like before.

** Z Carriage

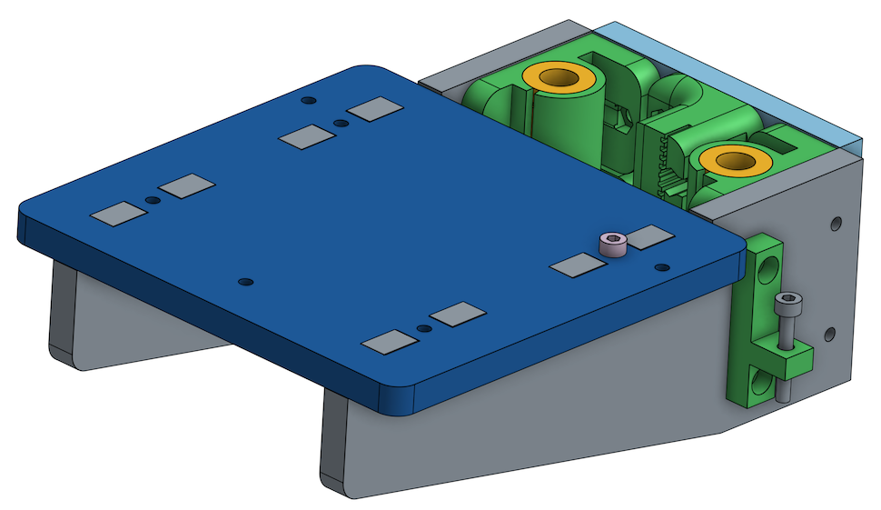
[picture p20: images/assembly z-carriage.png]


Parts:
 * 2 of Z lasercut Z side panels
 * lasercut Z top panel (has 8 rectangular holes and 4 round ones)
 * lasercut Z back panel
 * 4 of Printed Z bearing holder
 * Printed Z belt holder
 * Printed Z switch screw holder
 * 12 of M3 Hex Nut
 * 6 of M3x12 SHCS
 * 2 of M3x16 SHCS
 * 4 of M3x12 SHCS
 * about 18 inches (0.5 meter) of 6mm wide GT-2 Belt

Using a long bolt install 2 hex nuts into the traps on the belt
holder. 

Again, using the long bolt put 6 hex nuts into the traps on each of
the Z bearing holders.

Install one belt end in belt holder with pliers before assembling. The other belt end will be put in once both rod holders and the carriage are assembled.

[Don't fully tighten parts on back plate]

** Bed

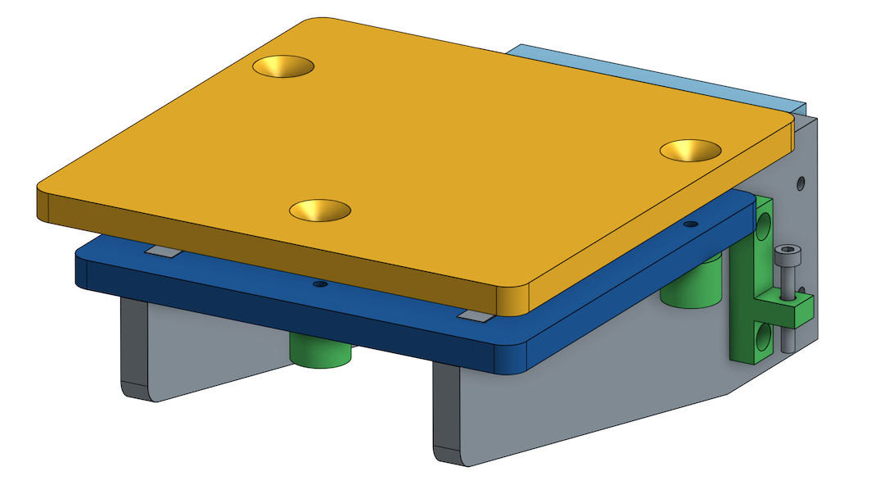
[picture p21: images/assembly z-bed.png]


Parts:
 * Lasercut print bed (only 3 holes)
 * 3 of M3x30 FHCS (Flat head countersunk screws)
 * 6 of M3 Hex Nut
 * 6 of M4 flat washer
 * 3 of Spring
 * 3 or Printed thumb nut adapter
 * Z carriage assembly
 * Blue tape

If not already countersunk, countersink the holes in the lasercut
plate so the screw heads are flush or slightly lower than the
surrounding wood.

Insert nuts into the 3 thumb nut adapters with the help of a longer
bolt.

Insert the flat head bolts through the lasercut piece and tighten a
hex nut on each bolt all the way up to the plate.

On each bolt, add a M4 washer, spring, then another washer, then the
lower Z assembly top plate then the thumb nut adapter. Tighten the
thumb nuts so the springs are about half way compressed.

** Z-Axis assembly in frame

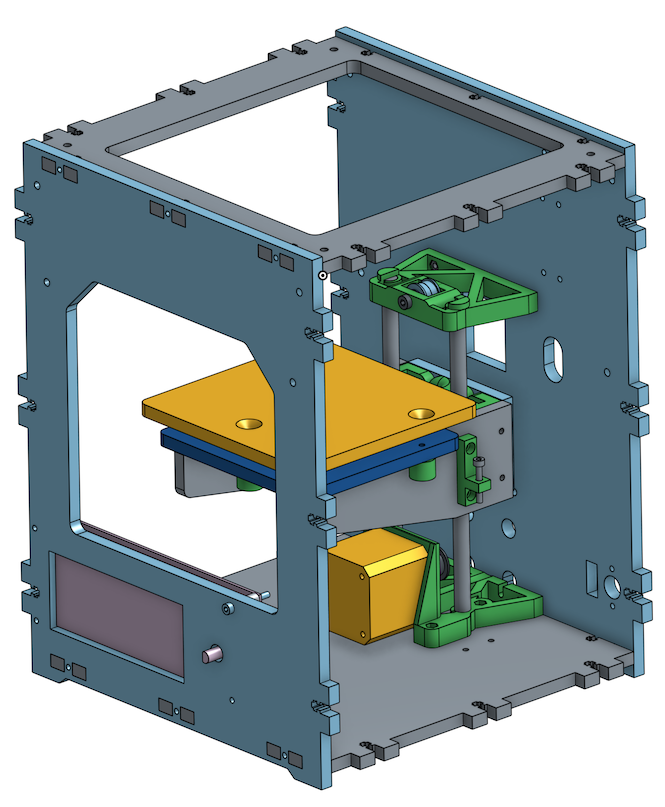
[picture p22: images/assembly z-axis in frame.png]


Parts:
 * 8 of M3x12 SHCS
 * 2 of 173mm 8mm smooth rod

Insert the rods into the idler and motor mounts. Loop the belt around the motor (slide the motor up first).

Bolt the Z motor mount and top mount into the frame.

Use pliers to install the other belt end. Loop the excess back and hold in place with a zip tie. Trim the zip tie.

Using M3 allen key through the holes in the back plate, tighten the screws on the back of the Z-carriage.

While pulling the motor downwards to tension the belt, tighten the motor screws to set the belt tension.

** Z-Axis homing switch

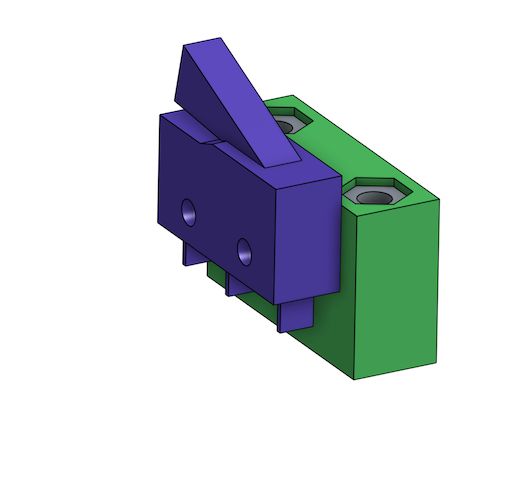
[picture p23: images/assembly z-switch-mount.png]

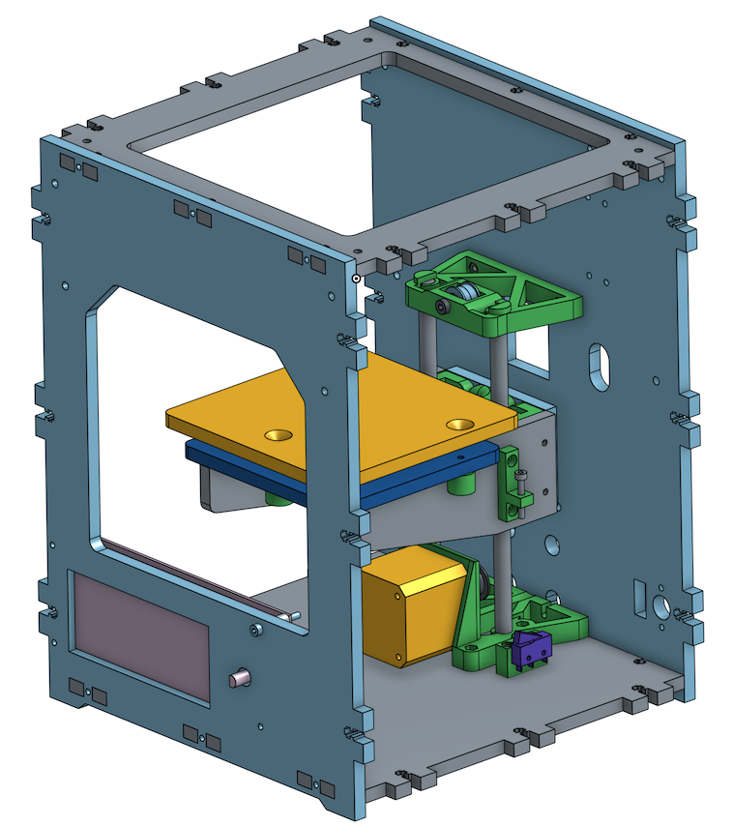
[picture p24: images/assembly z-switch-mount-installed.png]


Parts:
 * Printed Z homing switch mount
 * Homing Switch SS-5GL [with approximately 8 inches of wires]
 * 2 of #4-1/2" wood screw
 * 2 of M3 Hex Nut
 * 2 of M3x25 SHCS

Insert nuts into traps.

Run the wood screws through the homing switch into the plastic part.

Bolt into the bottom plate of box using M3x25 screws.

* XY Assembly
** AB Motor mounts

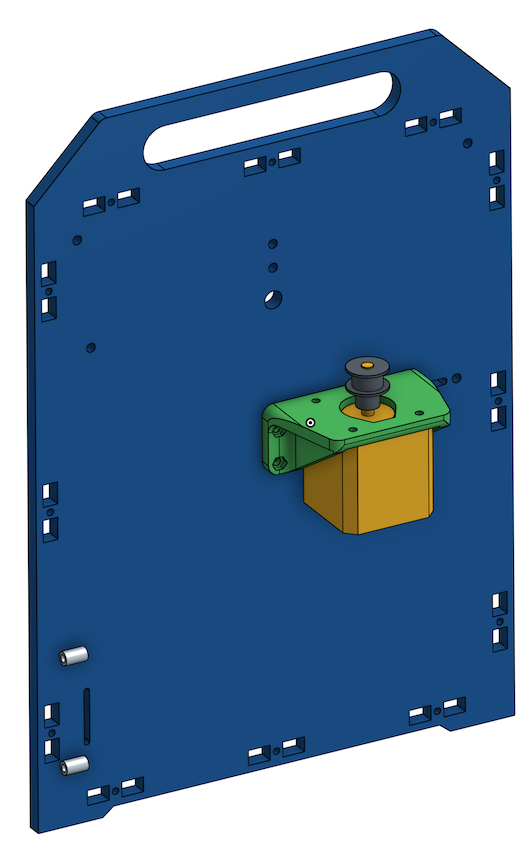
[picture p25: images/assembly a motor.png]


Parts:
 * Lasercut left panel
 * Lasercut right panel
 * 2 of Printed AB Motor Mount
 * 2 of NEMA17 Stepper Motor
 * 8 of M3 Hex Nut
 * 8 of M3x10 SHCS
 * 8 of M3x12 SHCS
 * 8 of M3 Flat Washer

Put M3 nuts in the nut traps.
 
Install a motor with pulley in each motor mount using the M3x10 SHCS
and flat washers.

Bolt the motor mounts, loosely, to the left and right side panels
using M3x12 SHCS. The slotted holes let us tension the short belts later.

** X-Ends

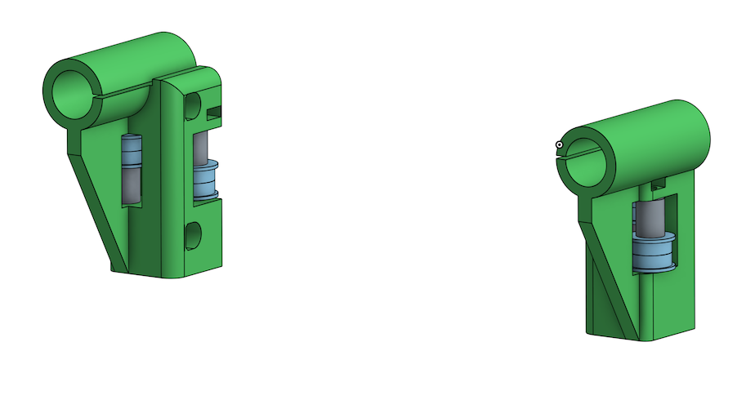
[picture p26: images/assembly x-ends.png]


Parts:
 * Printed Left X-End
 * Printed Right X-End
 * 8 of flanged 624 bearing for belt idler
 * 4 Printed X Idler Spacer (4mm hole, approx 11.6mm tall)
 * 2 of long LM8LUU Linear Bearing 8x15x45mm
 * 4 of M4 Hex Nut
 * 4 of M4 Flat Washer
 * 4 of M4x45 SHCS

Insert M4 nuts into nut traps.

Assemble the idlers as pictured. The idler stack is washer, bearing,
bearing then spacer. Make sure the spacers are on the correct side as pictured.

The belt-path on these parts should NOT be assembled as mirror images. 

[As long as both are assembled where each has one idler high, and the other low, and they are not built as mirror images you can assemble the rest fine]

** X Axis

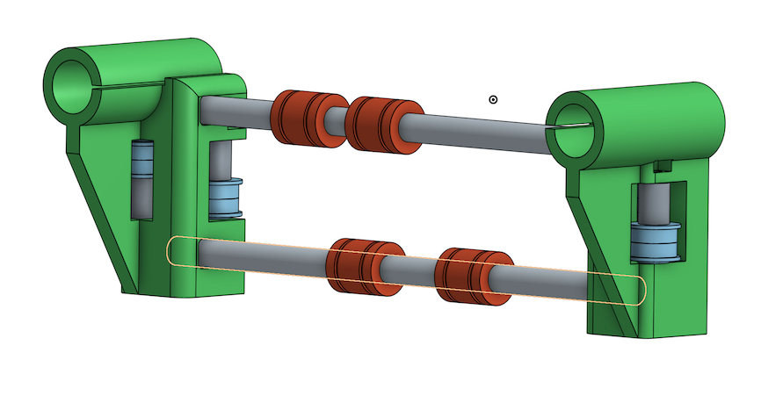
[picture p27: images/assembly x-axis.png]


Parts:
 * Left X-end assembly
 * Right X-end assembly
 * 4 of short LMS8UU 8x15x17
 * 2 of 8mm smooth rod 173mm long

Carefully put two LMS8UU linear bearings on each smooth rod.

Insert the rods into the holes on the side of one X-end, then put the
other X-end on the other side.

** Back short rods

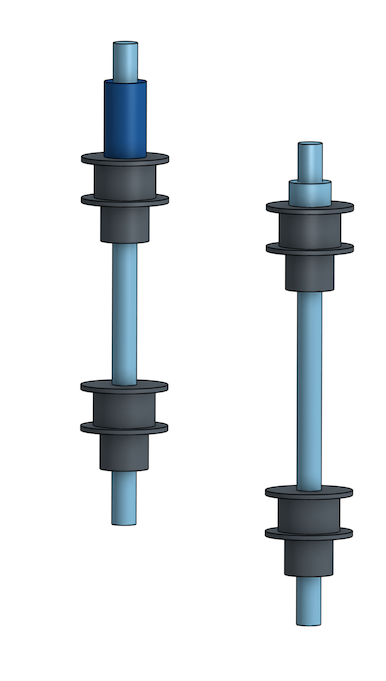
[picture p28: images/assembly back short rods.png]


Parts:
 * 2 of 5mm shaft, 100mm long
 * 4 of 20 tooth GT2 pulley
 * Printed pulley spacer (shorter, about 4.85mm long with 5mm bore)
 * Printed pulley spacer (longer, about 15.65mm long with 5mm bore)

Assemble the parts on the smooth rod as follows:
 * about 4mm of shaft bare
 * printed spacer
 * Pulley with belt closer to spacer. Tighten setscrews.
 * about 50mm of shaft bare
 * Pulley oriented in same direction. Leave setscrews slight loose, we
   will tighten them later.

One rod gets the longer spacer, and one the shorter spacer. 

Leave about 4mm of shaft sticking out of the spacer on one end of the shaft.

The pulley away from the spacer will be put in position later when
later parts are assembled.

** Back Lower short rod idlers

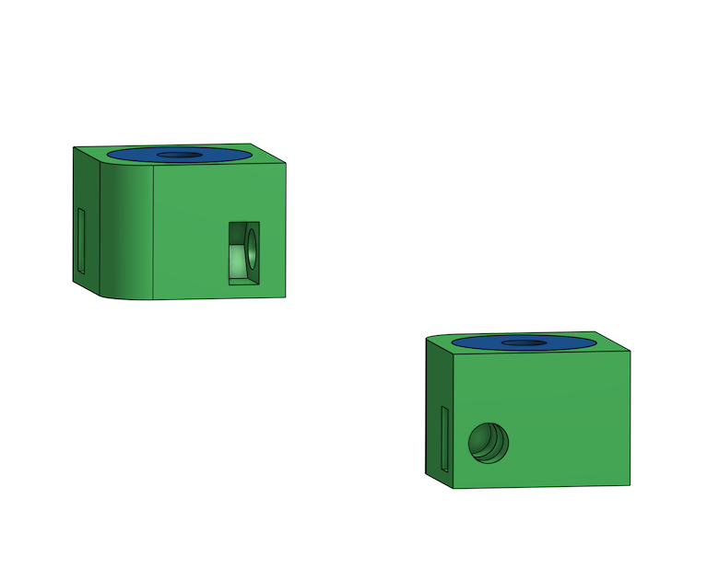
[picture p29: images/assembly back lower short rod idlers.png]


These parts go on the back of the machine and hold the lower end of
the short rods that drive the belts on the top.

Parts:
 * 2 of Printed Lower Rod Idler Holders
 * 4 of M4 hex nut
 * 2 of M4x14 SHCS
 * 2 of 625 roller bearing 5x16x6

Insert 625 bearing into hole by pressing them in. If they require more
force than you can do without tools, trim the hole with a hobby knife. Insert M4 nuts into traps.

Bolt to back panel using M4 bolts.

** Y Rod-holder back corners

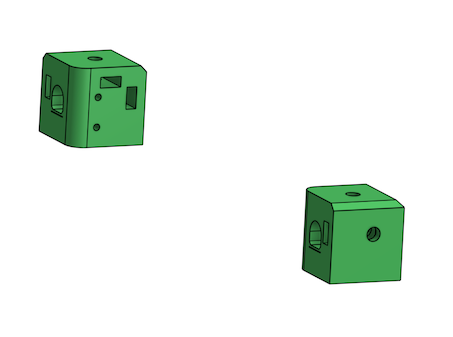
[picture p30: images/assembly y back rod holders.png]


Parts:
 * 2 of Printed top corner for pulley (has bearing indent and rod
   holder).
 * Homing switch SS-5GL [with approximately 14 inch of wires]
 * 2 of #4-1/2" wood screw
 * 6 of M4 Hex Nut
 * 2 of 625 roller bearing 5x16x6

Insert the M4 nuts for all the nut traps.

Install the 625 bearings in the bottom of the printed parts by
pressing them in by hand. Clean out the printed part with a hobby
knife if it's too tight.

Install the homing switch on the back left corner using the 1/2" long
wood screws.

** Y Rod-holder front corners and idlers

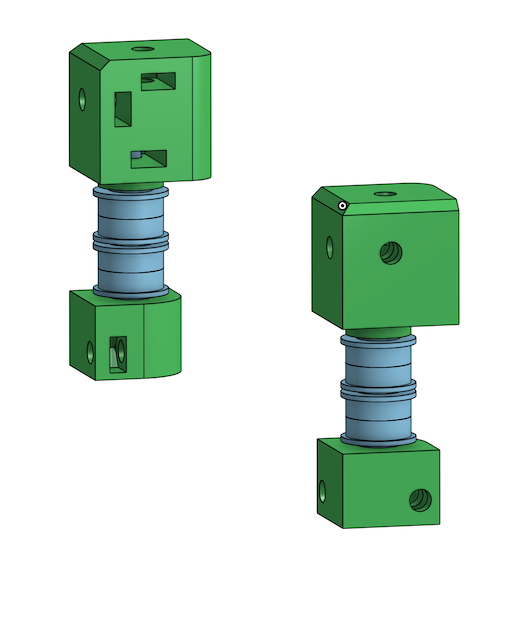
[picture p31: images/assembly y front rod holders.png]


Parts:
 * 2 of Printed top corner for idler (has 8mm rod hole and no hole for
   bearings to sit in)
 * 2 of Printed bottom corner for idler (again, no bearing indent in
   this part)
 * 10 of M4 hex nut
 * 2 of M4x40 SHCS
 * 8 of 624 flanged bearing for belt idler
 * 6 of M4 flat washer

Insert M4 captive nuts into printed parts.

Assemble belt idler bolts in following order:
 * Bolt (M4x40)
 * Lower printed part
 * M4 washer
 * pair of flanged 624 bearings (flanges on outside to keep belt in place)
 * M4 washer
 * pair of flanged 624 bearings
 * M4 washer
 * Upper corner printed part (bolt goes through the bottom hole into
   captive nut inside)

** X-carriage back

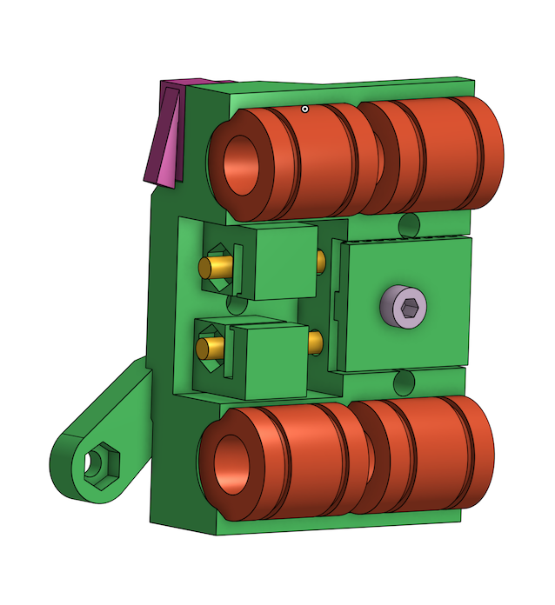
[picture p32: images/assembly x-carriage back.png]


The image above shows the bearings installed which does not happen in
this step.

Parts:
 * Printed X-Carriage back half
 * Homing switch small D2F-01L [with approximately 24-30 inches of wires]
 * 5015 12V blower fan [with approximately 24-30 inches of wires]
 * 7 of M3 Hex Nut
 * #4-1/2" wood screw
 * 2 M3x20 FHCS (countersunk)

Insert the M3 nuts into the nut traps:
 * 2 for fan mounting
 * 2 for duct mounting
 * 3 for x-carriage front mounting
 * 1 for x-belt clamp

Install the homing switch using a single 1/2" long #4 wood screw. Put
the screw closer to the top (where the motor will mount)

Bolt the fan on using the flat head screws.

** XY first assembly

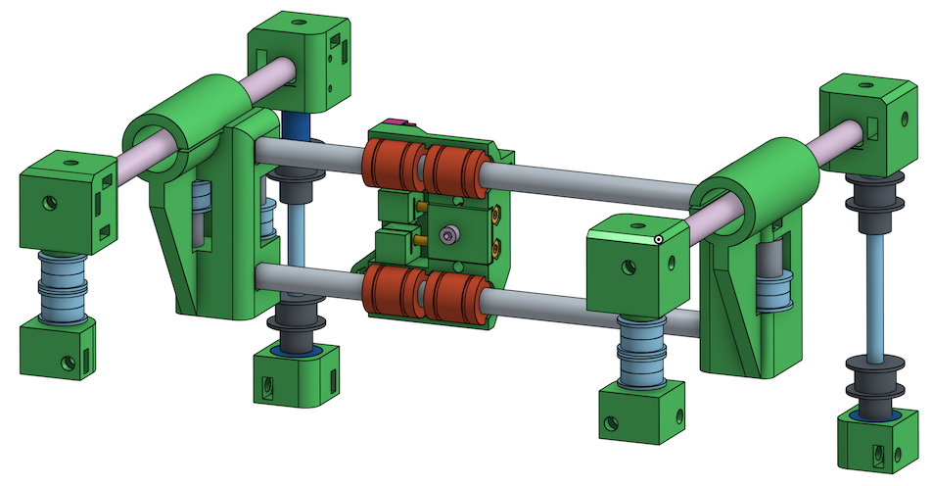
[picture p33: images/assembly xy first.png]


[get the Y rods into the Y ends and rod holders. Make sure the front
is the front and the left is the left. ]

Get the top plate and all XY parts.

Insert Y rods into bearings.

Insert 2 short LM8SUU bearings into each X rod. Insert X rods into X ends.

Put the Y ends on to the end of the Y rods. Bolt to top frame. 

Install the lower short rod holders in the back. Install the short rods, with a short closed loop belt loose around the shaft. [The tall spacer should go on the side where the X-end's outer idler is closer to the Y rods] Press up on the shaft while pushing down on the lower pulley and tighten the pulley setscrews to hold the rods in place.

[This is where you'd adjust alignment to get the Y frame to move smoothly]

Insert M3 captive nut into belt holders. This small part will hold one end of the belt and will be moved in/out to adjust belt tension. 

Insert one end of the belt into one part, threading the adjustment in only half way through the nut, and thread the belt through the full belt path, starting from the adjustable end, looping back around under the "fixed" clamp, then back through the other belt path to the other adjustable end. Once you've done this and made sure you didn't pull anything too tight, you can cut the belt in half and trim off the excess. There is room for about half an inch of excess on each belt length inside the X carriage.

** X carriage back on rails

Install the X carriage over the short bearings on the X rails. The
front half will clamp the bearings in place later, but first, the belts.

** XY assembly into frame

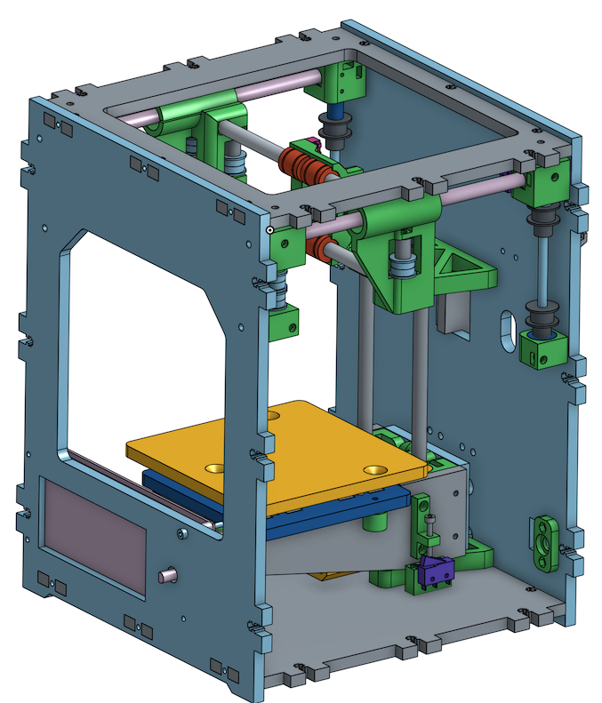
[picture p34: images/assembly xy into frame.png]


[insert into side of frame, bolt through the top]

[add the short rods with short belts]

** XY Belt

Parts:
 * Printed top and bottom belt holders (mirrored parts)
 * Printed Belt Clamp (flat on one side, ribbed on the other)
 * 2 of M3 hex nut
 * M3x16 SHCS
 * 2 of M3x35 SHCS

[The two belt paths as seen from the top of the machine when you're
facing the front wrap around a 'b' and 'd' shape. It doesn't matter
which is the top belt or the bottom, but the idlers on the X ends need
to be configured for what you've chosen. My CAD drawings have the 'd'
belt on top, and 'b' on the bottom.]

Start by using pliers to insert one end of the belt into the top belt
holder.

Insert a M3 nut into the nut trap and install on the X carriage by
threading the M3x35 bolt through the hole into the carriage and into
the nut on the far side of the belt holder. Only tighten the screw
enough to thread through the nut, the rest of the thread is used to
adjust the belt tension.

Feed the belt through the belt path for the upper belt
(counter-clockwise around a 'd' if you're following the CAD drawings)
and back to the other side of the X carriage.

Insert the M3x16 screw through the flat side of the belt
clamp. Take the belt that's now feeding into the right side of the
X-carriage and put it under the clamp and loop the belt back out the
right side of the X carriage for the bottom portion of the belt path.

Route the belt through the lower belt path (clockwise around a 'b' if
you're following the CAD drawing). Using pliers, insert the other end
of the belt into the other belt holder like the first one. Install a
M3 nut into the belt holder and bolt into the lower portion of the
X-carriage using another M3x35 going through the x-carriage and into
the nut as before.

I expect the belt is a bit loose at this point, so before using the
adjustment on the M3x35mm screws, loosen the M3x16 going through the
rectangular clamp where the belt does a U-turn and pull on the belt to
get both belts on but not super tight with about the same tension.

Verify your belts are all routed correctly, for example not falling
off the side of pulleys or idlers. 

At this point, I expect the belts to be on tight enough to not fall
off but not tight enough to make a note when plucked. Also, the nuts
on the left side of the x-carriage (as you're facing the front of the
machine) should have only the tip of M3x35mm screw poking through so
we can adjust the belts tighter later. If you need to adjust the
belts, loosen the part where the belts U-turn to loosen the belts then
put them back.

(the slit in the X-end belt holders that slide onto the belt should
face towards the center of the two belts)

** X carriage front

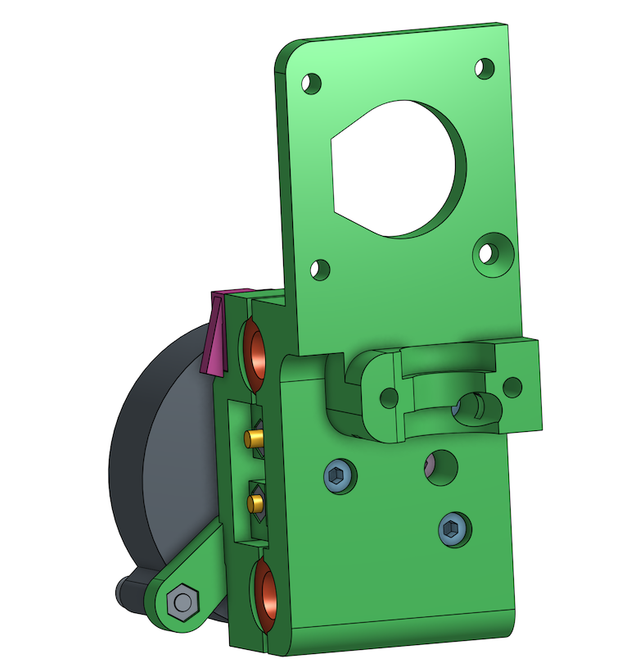
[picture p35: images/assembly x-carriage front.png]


Parts:
 * Printed X-Carriage Front
 * 3 of M3x25 SHCS
 * 2 of M3 Hex Nut

Insert M3 nuts into the traps for the hotend groove mount.

Using 3 M3x25 SHCS and an allen key, attach the front half of the
X-Carriage to the back half. Make sure the linear bearings are all
seated well before tightening the screws. Don't over-tigthen the
screws.

** E3d hotend

[assemble the e3d hotend, fan on fan duct. the teflon tube should
stick out [3 inches]. Will be trimmed further when installing on extruder]

[the heater cartridge shouldn't stick more than 1.5mm out of the end of
the heater block]

** Extruder Plate

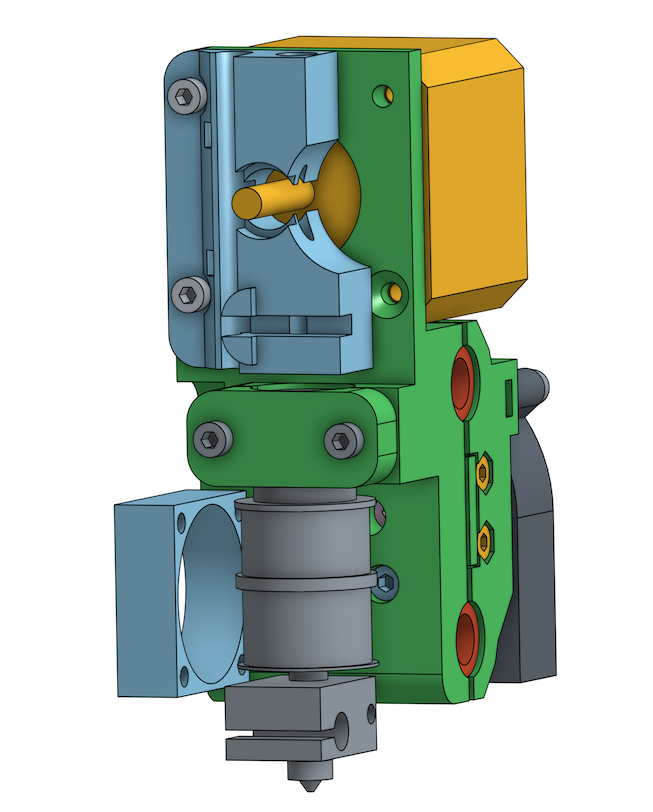
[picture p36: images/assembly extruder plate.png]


Parts:
 * Printed Extruder Plate
 * Printed Hotend Clamp
 * 2 of M3x20 SHCS
 * M3x8 flat head (countersunk) screw
 * 2 of M3x12 SHCS
 * NEMA17 Stepper for extruder
 * Extruder filament drive gear
 * e3d v6 assembly with at least 3 inches of filament guide tube
 * Hobby knife with sharp blade

Attach the NEMA17 motor and extruder plate to the front of the
X-carriage using the M3x12 screws.

Insert the filament tube of the hotend into the extruder plate. It
should be too long and stick out past where the filament drive gear
is. 

Insert the groove into the groove clamp and trim off the excess
filament guide tube around the printed part. Clamp down the groove
mount with the printed clamp and two M3x20 SHCS.

Install the filament drive gear on the motor shaft with the setscrew
futher away from the motor. Align the setscrew on the flat of the
motor shaft, and the filament teeth with the filament path, and
tighten the drive gear setscrew.

** Extruder Idler lever

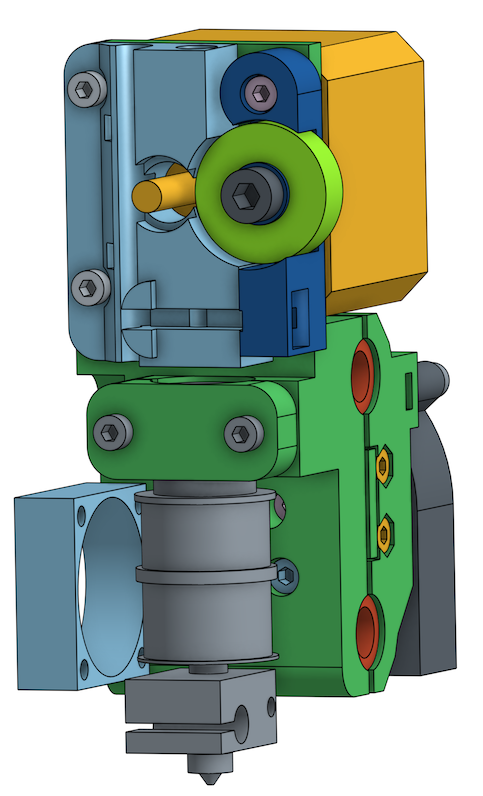
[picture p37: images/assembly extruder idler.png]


Parts:
 * Printed Extruder Idler
 * 608 Skate bearing 8x22x7
 * M3x16 SHCS
 * M5x10
 * M5 Flat Washer

Insert the 608 bearing over the post on the printed extruder
idler. Secure the 608 bearing on the printed part with the M5 bolt and
washer.

Install the extruder idler on the top right screw of the extruder
motor using the M3x16 screw. Only lightly tighten this screw so the
idler can still rotate in and out.

Bolt the 608 bearing to the extruder idler. assemble the bolt that
sets the idler tension.]

** Extruder Idler Bolt

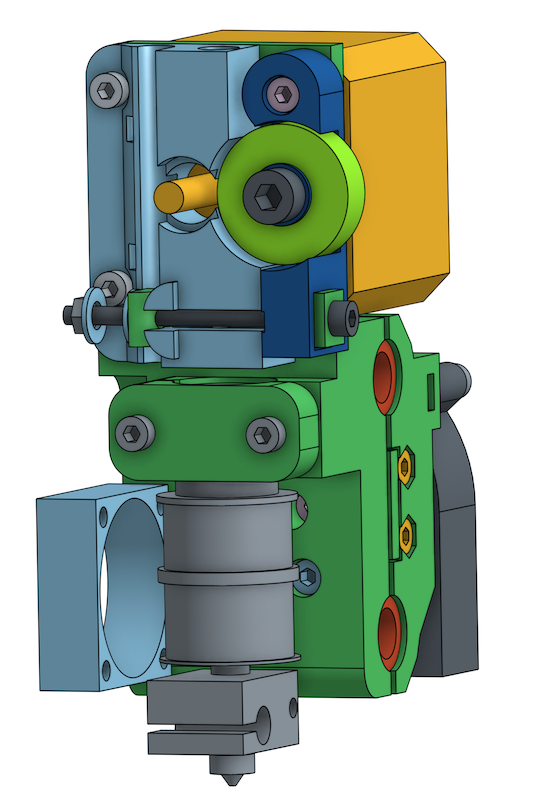
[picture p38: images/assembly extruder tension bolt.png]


Parts:
 * 2 of Printed Idler Pivot (small half cylinder things with a
   circular hole in the flat face)
 * M3x45 bolt
 * M3 hex nut
 * Extruder Spring
 * 2 of M4 flat washer
 * A couple feet of piece of PLA filament.

Insert the long bolt through the flat face of the pivot, through the
extruder idler lever, then through the round face of the pivot,
washer, spring, washer then m3 nut.

The second pivot snaps on to the front face of the extruder.

Feed some filmaent into the top of the extruder through the idler. You
should be able to push it enough to move the filament idler back, but
when you pull the filament back out it should not be flattened by the
pressure. Having small teeth marks and a thin flat on the opposite
side is about the right amount of tension.

** Blower

Parts:
 * 5015 blower
 * 2 of M3x20 screws (preferably flat head/countersunk)

Install the blower on the back of the X-carriage with M3x20 screws.

** Blower Duct

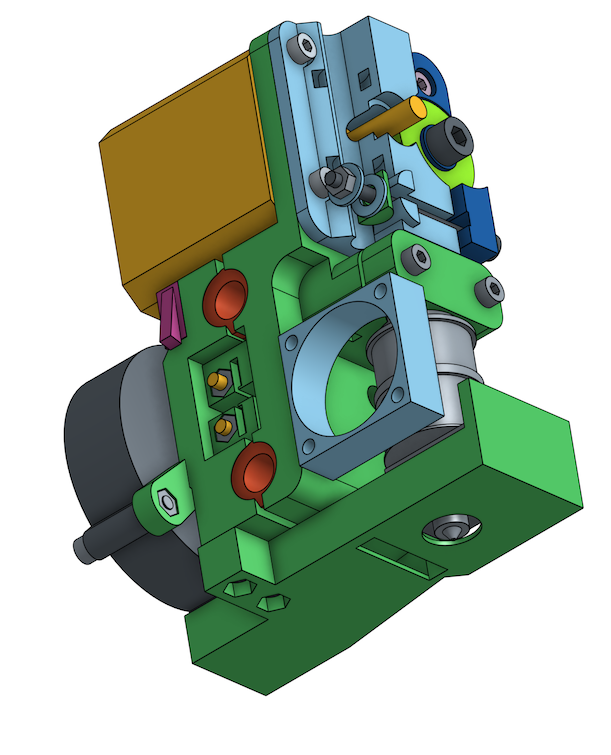
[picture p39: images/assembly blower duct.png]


Parts:
 * Printed blower duct
 * Aluminum foil tape
 * 2 of M3x10 SHCS
 * hobby knife

[put aluminum foil tape on the top next to where the heater block
goes, and on the bottom to make it easier to clean when melted plastic
tries to stick to it. Trim foil with hobby knife for nozzle
hole. Attach to x carriage with M3 bolts. verify heater cartridge,
clamp screw, and other hot parts have gap away from foil
tape. They will conduct heat into plastic part.]

* Frame Left/right

Mount printrboard on the inside of the right frame

Wire up everything (homing switches, wires going out the back, motors, power-input, LCD).

The power switch mount holder bolts to the back of the frame.

Bolt on the left side frame. loop the short belt around the motor pulley. Pull the motor towards the front of the printer to set the belt tension, and while holding it there tighten the 4 screws holding the motor in place on the left plate.

Do the same on the right plate.

* Odds and ends

Wire extensions?

Install filament guide mount and wire guide (bolts go from inside of printer into printed part)

Install filament guide tube between tube mount and extruder. This is not held in when there's no filament installed so it can easily come out to change filament.

Install knob on front of LCD to suit your tastes.

Install spool holder. Insert tab into hole on back, lift part upwards and rotate into place. This removes easily for travel.

** Lights?

[yeah, you can install lights]

* First Print
Lots to write up here:
 * Adjust the tension on the filament idler nut so that the filament
   doesn't end up with a large flat on one side if you take it back
   out of the extruder.
 * Adjust homing position at bottom so z-carriage barely doesn't
   bottom out
 * Adjust bed position to be very low.
 * Jog from Z home to Z of 0 slowly to not crash into nozzle.
 * Adjust bed to be near nozzle and level.
 * Optional?: Adjust z-height in firmware.

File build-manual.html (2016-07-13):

# build-manual

## Table of Contents

- 1. SBHXY Build Manual
- 2. Common Build Hints
  - 2.1. Captive Nuts
  - 2.2. "Tightness"
  - 2.3. [fitting laser slots together]
- 3. Assembly Instructions
- 4. Front Panel
- 5. Frame "Skeleton"
- 6. Z-Axis
  - 6.1. Z Motor mount
  - 6.2. Z Idler
  - 6.3. Z Carriage
  - 6.4. Bed
  - 6.5. Z-Axis assembly in frame
  - 6.6. Z-Axis homing switch
- 7. XY Assembly
  - 7.1. AB Motor mounts
  - 7.2. X-Ends
  - 7.3. X Axis
  - 7.4. Back short rods
  - 7.5. Back Lower short rod idlers
  - 7.6. Y Rod-holder back corners
  - 7.7. Y Rod-holder front corners and idlers
  - 7.8. X-carriage back
  - 7.9. XY first assembly
  - 7.10. X carriage back on rails
  - 7.11. XY assembly into frame
  - 7.12. XY Belt
  - 7.13. X carriage front
  - 7.14. E3d hotend
  - 7.15. Extruder Plate
  - 7.16. Extruder Idler lever
  - 7.17. Extruder Idler Bolt
  - 7.18. Blower
  - 7.19. Blower Duct
- 8. Frame Left/right
- 9. Odds and ends
  - 9.1. Lights?
- 10. First Print

## 1 SBHXY Build Manual

This is the build manual for the SBHXY.



## 2 Common Build Hints

There are a couple of things that make easier.

### 2.1 Captive Nuts

Captive nuts that go flat into a part are easier to insert using a longer bolt to push them in.

Captive nuts that go in sideways fit in with the point first into the part and are easier to insert with pliers. Once you get it started use the tips of your pliers to push the nut in the rest of the way.

### 2.2 "Tightness"

[don't over tighten bolts. Most of the nuts on this printer sit in printed parts or wood which will colapse or deform when over-tightened which may prevent you from disassembling it later and will end up looser than tightening the screws "just enough"]

[how do you know how much is enough?]

### 2.3 [fitting laser slots together]

[these might be tight. If you hammer them or pull unevenly apart the melamine kind of delaminates.]

## 3 Assembly Instructions

## 4 Front Panel

assembly front-panel.png

Parts:

- Lasercut front panel
- 4 of M3x25 SHCS
- 4 of 10mm spacer with 3mm hole
- 4 of M3 nylon lock nut
- RepRapDiscount Smart Controller or clone
- Optional: foam or foam tape, approximately 3mm thick

If your LCD is loose from the back PCB of the LCD, it will vibrate and make noise. Put foam between the two.

Install the LCD with 10mm spacers and M3x25 and lock nuts. The LCD will be on the lower left corner as viewed from the front of the machine, with the SD card sticking out to the left and the knob on the right of the LCD.

## 5 Frame "Skeleton"

assembly frame-skeleton.png

Parts:

- Lasercut front panel (with LCD installed)
- Lasercut bottom panel
- Lasercut back panel
- Lasercut top panel
- 12 of M3 hex nut
- 12 of M3x12 SHCS

Assemble the following frame pieces: Top, Front, Bottom, Back. M3 nuts are inserted into the traps then M3x12 bolts go through front and back panels to hold the pieces together.

The bottom panel has the holes towards the back of the machine, with the pair of non-symetrical holes on the right as the assembled machine is viewed from the front. These holes mount the Z homing switch.

The back panel has a slot near the top corner, this also goes towards the right as viewed from the front of the assembled machine.

The top panel is the same in every direction.

## 6 Z-Axis

### 6.1 Z Motor mount

assembly z-bottom-motor.png

Parts:

- Printed Z motor mount
- 6 of M3 hex nuts
- 4 of M3x10 SHCS
- NEMA17 Stepper Motor
- GT2 Belt Pulley, 20 teeth with setscrews

Install the 6 M3 hex nuts into the traps using longer M3 bolts. The ones going through the side of the printed part are easier to install by putting the long bolt through, then threading the nut on, then pulling bolt to seat the nut, then unscrewing the bolt.

### 6.2 Z Idler

assembly z-top-rodholder.png

Parts:

- Printed Z idler mount
- 2 of 624 Flanged bearings
- M4x20 SHCS
- M4 hex nut
- 2 of M4 flat Washer

Insert the washers on the outside, bearing pair in the middle into the hole for the belt idler, insert the nut and bolt. The bearings should spin easily, and not be loose between the printed part to slide along the bolt.

Insert the two M3 nuts into the nut traps using longer bolts to pull them in place like before.

### 6.3 Z Carriage

assembly z-carriage.png

Parts:

- 2 of Z lasercut Z side panels
- lasercut Z top panel (has 8 rectangular holes and 4 round ones)
- lasercut Z back panel
- 4 of Printed Z bearing holder
- Printed Z belt holder
- Printed Z switch screw holder
- 12 of M3 Hex Nut
- 6 of M3x12 SHCS
- 2 of M3x16 SHCS
- 4 of M3x12 SHCS
- about 18 inches (0.5 meter) of 6mm wide GT-2 Belt

Using a long bolt install 2 hex nuts into the traps on the belt holder.

Again, using the long bolt put 6 hex nuts into the traps on each of the Z bearing holders.

Install one belt end in belt holder with pliers before assembling. The other belt end will be put in once both rod holders and the carriage are assembled.

[Don't fully tighten parts on back plate]

### 6.4 Bed

assembly z-bed.png

Parts:

- Lasercut print bed (only 3 holes)
- 3 of M3x30 FHCS (Flat head countersunk screws)
- 6 of M3 Hex Nut
- 6 of M4 flat washer
- 3 of Spring
- 3 or Printed thumb nut adapter
- Z carriage assembly
- Blue tape

If not already countersunk, countersink the holes in the lasercut plate so the screw heads are flush or slightly lower than the surrounding wood.

Insert nuts into the 3 thumb nut adapters with the help of a longer bolt.

Insert the flat head bolts through the lasercut piece and tighten a hex nut on each bolt all the way up to the plate.

On each bolt, add a M4 washer, spring, then another washer, then the lower Z assembly top plate then the thumb nut adapter. Tighten the thumb nuts so the springs are about half way compressed.

### 6.5 Z-Axis assembly in frame

assembly z-axis in frame.png

Parts:

- 8 of M3x12 SHCS
- 2 of 173mm 8mm smooth rod

Insert the rods into the idler and motor mounts. Loop the belt around the motor (slide the motor up first).

Bolt the Z motor mount and top mount into the frame.

Use pliers to install the other belt end. Loop the excess back and hold in place with a zip tie. Trim the zip tie.

Using M3 allen key through the holes in the back plate, tighten the screws on the back of the Z-carriage.

While pulling the motor downwards to tension the belt, tighten the motor screws to set the belt tension.

### 6.6 Z-Axis homing switch

assembly z-switch-mount.png assembly z-switch-mount-installed.png

Parts:

- Printed Z homing switch mount
- Homing Switch SS-5GL [with approximately 8 inches of wires]
- 2 of #4-1/2" wood screw
- 2 of M3 Hex Nut
- 2 of M3x25 SHCS

Insert nuts into traps.

Run the wood screws through the homing switch into the plastic part.

Bolt into the bottom plate of box using M3x25 screws.

## 7 XY Assembly

### 7.1 AB Motor mounts

assembly a motor.png

Parts:

- Lasercut left panel
- Lasercut right panel
- 2 of Printed AB Motor Mount
- 2 of NEMA17 Stepper Motor
- 8 of M3 Hex Nut
- 8 of M3x10 SHCS
- 8 of M3x12 SHCS
- 8 of M3 Flat Washer

Put M3 nuts in the nut traps.

Install a motor with pulley in each motor mount using the M3x10 SHCS and flat washers.

Bolt the motor mounts, loosely, to the left and right side panels using M3x12 SHCS. The slotted holes let us tension the short belts later.

### 7.2 X-Ends

assembly x-ends.png

Parts:

- Printed Left X-End
- Printed Right X-End
- 8 of flanged 624 bearing for belt idler
- 4 Printed X Idler Spacer (4mm hole, approx 11.6mm tall)
- 2 of long LM8LUU Linear Bearing 8x15x45mm
- 4 of M4 Hex Nut
- 4 of M4 Flat Washer
- 4 of M4x45 SHCS

Insert M4 nuts into nut traps.

Assemble the idlers as pictured. The idler stack is washer, bearing, bearing then spacer. Make sure the spacers are on the correct side as pictured.

The belt-path on these parts should NOT be assembled as mirror images.

[As long as both are assembled where each has one idler high, and the other low, and they are not built as mirror images you can assemble the rest fine]

### 7.3 X Axis

assembly x-axis.png

Parts:

- Left X-end assembly
- Right X-end assembly
- 4 of short LMS8UU 8x15x17
- 2 of 8mm smooth rod 173mm long

Carefully put two LMS8UU linear bearings on each smooth rod.

Insert the rods into the holes on the side of one X-end, then put the other X-end on the other side.

### 7.4 Back short rods

assembly back short rods.png

Parts:

- 2 of 5mm shaft, 100mm long
- 4 of 20 tooth GT2 pulley
- Printed pulley spacer (shorter, about 4.85mm long with 5mm bore)
- Printed pulley spacer (longer, about 15.65mm long with 5mm bore)

Assemble the parts on the smooth rod as follows:

- about 4mm of shaft bare
- printed spacer
- Pulley with belt closer to spacer. Tighten setscrews.
- about 50mm of shaft bare
- Pulley oriented in same direction. Leave setscrews slight loose, we will tighten them later.

One rod gets the longer spacer, and one the shorter spacer.

Leave about 4mm of shaft sticking out of the spacer on one end of the shaft.

The pulley away from the spacer will be put in position later when later parts are assembled.

### 7.5 Back Lower short rod idlers

assembly back lower short rod idlers.png

These parts go on the back of the machine and hold the lower end of the short rods that drive the belts on the top.

Parts:

- 2 of Printed Lower Rod Idler Holders
- 4 of M4 hex nut
- 2 of M4x14 SHCS
- 2 of 625 roller bearing 5x16x6

Insert 625 bearing into hole by pressing them in. If they require more force than you can do without tools, trim the hole with a hobby knife. Insert M4 nuts into traps.

Bolt to back panel using M4 bolts.

### 7.6 Y Rod-holder back corners

assembly y back rod holders.png

Parts:

- 2 of Printed top corner for pulley (has bearing indent and rod holder).
- Homing switch SS-5GL [with approximately 14 inch of wires]
- 2 of #4-1/2" wood screw
- 6 of M4 Hex Nut
- 2 of 625 roller bearing 5x16x6

Insert the M4 nuts for all the nut traps.

Install the 625 bearings in the bottom of the printed parts by pressing them in by hand. Clean out the printed part with a hobby knife if it's too tight.

Install the homing switch on the back left corner using the 1/2" long wood screws.

### 7.7 Y Rod-holder front corners and idlers

assembly y front rod holders.png

Parts:

- 2 of Printed top corner for idler (has 8mm rod hole and no hole for bearings to sit in)
- 2 of Printed bottom corner for idler (again, no bearing indent in this part)
- 10 of M4 hex nut
- 2 of M4x40 SHCS
- 8 of 624 flanged bearing for belt idler
- 6 of M4 flat washer

Insert M4 captive nuts into printed parts.

Assemble belt idler bolts in following order:

- Bolt (M4x40)
- Lower printed part
- M4 washer
- pair of flanged 624 bearings (flanges on outside to keep belt in place)
- M4 washer
- pair of flanged 624 bearings
- M4 washer
- Upper corner printed part (bolt goes through the bottom hole into captive nut inside)

### 7.8 X-carriage back

assembly x-carriage back.png

The image above shows the bearings installed which does not happen in this step.

Parts:

- Printed X-Carriage back half
- Homing switch small D2F-01L [with approximately 24-30 inches of wires]
- 5015 12V blower fan [with approximately 24-30 inches of wires]
- 7 of M3 Hex Nut
- #4-1/2" wood screw
- 2 M3x20 FHCS (countersunk)

Insert the M3 nuts into the nut traps:

- 2 for fan mounting
- 2 for duct mounting
- 3 for x-carriage front mounting
- 1 for x-belt clamp

Install the homing switch using a single 1/2" long #4 wood screw. Put the screw closer to the top (where the motor will mount)

Bolt the fan on using the flat head screws.

### 7.9 XY first assembly

assembly xy first.png

[get the Y rods into the Y ends and rod holders. Make sure the front is the front and the left is the left. ]

Get the top plate and all XY parts.

Insert Y rods into bearings.

Insert 2 short LM8SUU bearings into each X rod. Insert X rods into X ends.

Put the Y ends on to the end of the Y rods. Bolt to top frame.

Install the lower short rod holders in the back. Install the short rods, with a short closed loop belt loose around the shaft. [The tall spacer should go on the side where the X-end's outer idler is closer to the Y rods] Press up on the shaft while pushing down on the lower pulley and tighten the pulley setscrews to hold the rods in place.

[This is where you'd adjust alignment to get the Y frame to move smoothly]

Insert M3 captive nut into belt holders. This small part will hold one end of the belt and will be moved in/out to adjust belt tension.

Insert one end of the belt into one part, threading the adjustment in only half way through the nut, and thread the belt through the full belt path, starting from the adjustable end, looping back around under the "fixed" clamp, then back through the other belt path to the other adjustable end. Once you've done this and made sure you didn't pull anything too tight, you can cut the belt in half and trim off the excess. There is room for about half an inch of excess on each belt length inside the X carriage.

### 7.10 X carriage back on rails

Install the X carriage over the short bearings on the X rails. The front half will clamp the bearings in place later, but first, the belts.

### 7.11 XY assembly into frame

assembly xy into frame.png

[insert into side of frame, bolt through the top]

[add the short rods with short belts]

### 7.12 XY Belt

Parts:

- Printed top and bottom belt holders (mirrored parts)
- Printed Belt Clamp (flat on one side, ribbed on the other)
- 2 of M3 hex nut
- M3x16 SHCS
- 2 of M3x35 SHCS

[The two belt paths as seen from the top of the machine when you're facing the front wrap around a 'b' and 'd' shape. It doesn't matter which is the top belt or the bottom, but the idlers on the X ends need to be configured for what you've chosen. My CAD drawings have the 'd' belt on top, and 'b' on the bottom.]

Start by using pliers to insert one end of the belt into the top belt holder.

Insert a M3 nut into the nut trap and install on the X carriage by threading the M3x35 bolt through the hole into the carriage and into the nut on the far side of the belt holder. Only tighten the screw enough to thread through the nut, the rest of the thread is used to adjust the belt tension.

Feed the belt through the belt path for the upper belt (counter-clockwise around a 'd' if you're following the CAD drawings) and back to the other side of the X carriage.

Insert the M3x16 screw through the flat side of the belt clamp. Take the belt that's now feeding into the right side of the X-carriage and put it under the clamp and loop the belt back out the right side of the X carriage for the bottom portion of the belt path.

Route the belt through the lower belt path (clockwise around a 'b' if you're following the CAD drawing). Using pliers, insert the other end of the belt into the other belt holder like the first one. Install a M3 nut into the belt holder and bolt into the lower portion of the X-carriage using another M3x35 going through the x-carriage and into the nut as before.

I expect the belt is a bit loose at this point, so before using the adjustment on the M3x35mm screws, loosen the M3x16 going through the rectangular clamp where the belt does a U-turn and pull on the belt to get both belts on but not super tight with about the same tension.

Verify your belts are all routed correctly, for example not falling off the side of pulleys or idlers.

At this point, I expect the belts to be on tight enough to not fall off but not tight enough to make a note when plucked. Also, the nuts on the left side of the x-carriage (as you're facing the front of the machine) should have only the tip of M3x35mm screw poking through so we can adjust the belts tighter later. If you need to adjust the belts, loosen the part where the belts U-turn to loosen the belts then put them back.

(the slit in the X-end belt holders that slide onto the belt should face towards the center of the two belts)

### 7.13 X carriage front

assembly x-carriage front.png

Parts:

- Printed X-Carriage Front
- 3 of M3x25 SHCS

Using 3 M3x25 SHCS and an allen key, attach the front half of the X-Carriage to the back half. Make sure the linear bearings are all seated well before tightening the screws. Don't over-tigthen the screws.

### 7.14 E3d hotend

[assemble the e3d hotend, fan on fan duct. the teflon tube should stick out [3 inches]. Will be trimmed further when installing on extruder]

[the heater cartridge shouldn't stick more than 1.5mm out of the end of the heater block]

### 7.15 Extruder Plate

assembly extruder plate.png

Parts:

- Printed Extruder Plate
- Printed Hotend Clamp
- 2 of M3x20 SHCS
- M3x8 flat head (countersunk) screw
- 2 of M3x12 SHCS
- NEMA17 Stepper for extruder
- Extruder filament drive gear
- e3d v6 assembly with at least 3 inches of filament guide tube
- Hobby knife with sharp blade

Attach the NEMA17 motor and extruder plate to the front of the X-carriage using the M3x12 screws.

Insert the filament tube of the hotend into the extruder plate. It should be too long and stick out past where the filament drive gear is.

Insert the groove into the groove clamp and trim off the excess filament guide tube around the printed part. Clamp down the groove mount with the printed clamp and two M3x20 SHCS.

Install the filament drive gear on the motor shaft with the setscrew futher away from the motor. Align the setscrew on the flat of the motor shaft, and the filament teeth with the filament path, and tighten the drive gear setscrew.

### 7.16 Extruder Idler lever

assembly extruder idler.png

Parts:

- Printed Extruder Idler
- 608 Skate bearing 8x22x7
- M3x16 SHCS
- M5x10
- M5 Flat Washer

Insert the 608 bearing over the post on the printed extruder idler. Secure the 608 bearing on the printed part with the M5 bolt and washer.

Install the extruder idler on the top right screw of the extruder motor using the M3x16 screw. Only lightly tighten this screw so the idler can still rotate in and out.

Bolt the 608 bearing to the extruder idler. assemble the bolt that sets the idler tension.]

### 7.17 Extruder Idler Bolt

assembly extruder tension bolt.png

Parts:

- 2 of Printed Idler Pivot (small half cylinder things with a circular hole in the flat face)
- M3x45 bolt
- M3 hex nut
- Extruder Spring
- 2 of M4 flat washer
- A couple feet of piece of PLA filament.

Insert the long bolt through the flat face of the pivot, through the extruder idler lever, then through the round face of the pivot, washer, spring, washer then m3 nut.

The second pivot snaps on to the front face of the extruder.

Feed some filmaent into the top of the extruder through the idler. You should be able to push it enough to move the filament idler back, but when you pull the filament back out it should not be flattened by the pressure. Having small teeth marks and a thin flat on the opposite side is about the right amount of tension.

### 7.18 Blower

Parts:

- 5015 blower
- 2 of M3x20 screws (preferably flat head/countersunk)

Install the blower on the back of the X-carriage with M3x20 screws.

### 7.19 Blower Duct

assembly blower duct.png

Parts:

- Printed blower duct
- Aluminum foil tape
- 2 of M3x10 SHCS
- hobby knife

[put aluminum foil tape on the top next to where the heater block goes, and on the bottom to make it easier to clean when melted plastic tries to stick to it. Trim foil with hobby knife for nozzle hole. Attach to x carriage with M3 bolts. verify heater cartridge, clamp screw, and other hot parts have gap away from foil tape. They will conduct heat into plastic part.]

## 8 Frame Left/right

Mount printrboard on the inside of the right frame

Wire up everything (homing switches, wires going out the back, motors, power-input, LCD).

The power switch mount holder bolts to the back of the frame.

Bolt on the left side frame. loop the short belt around the motor pulley. Pull the motor towards the front of the printer to set the belt tension, and while holding it there tighten the 4 screws holding the motor in place on the left plate.

Do the same on the right plate.

## 9 Odds and ends

Wire extensions?

Install filament guide mount and wire guide (bolts go from inside of printer into printed part)

Install filament guide tube between tube mount and extruder. This is not held in when there's no filament installed so it can easily come out to change filament.

Install knob on front of LCD to suit your tastes.

Install spool holder. Insert tab into hole on back, lift part upwards and rotate into place. This removes easily for travel.

### 9.1 Lights?

[yeah, you can install lights]

## 10 First Print

Lots to write up here:

- Adjust the tension on the filament idler nut so that the filament doesn't end up with a large flat on one side if you take it back out of the extruder.
- Adjust homing position at bottom so z-carriage barely doesn't bottom out
- Adjust bed position to be very low.
- Jog from Z home to Z of 0 slowly to not crash into nozzle.
- Adjust bed to be near nozzle and level.
- Optional?: Adjust z-height in firmware.

Author: Nick Winters

Created: 2016-07-13 Wed 14:36

Emacs (http://www.gnu.org/software/emacs/) 24.4.51.2 (Org (http://orgmode.org) mode 8.2.10)

Validate (http://validator.w3.org/check?uri=referer)

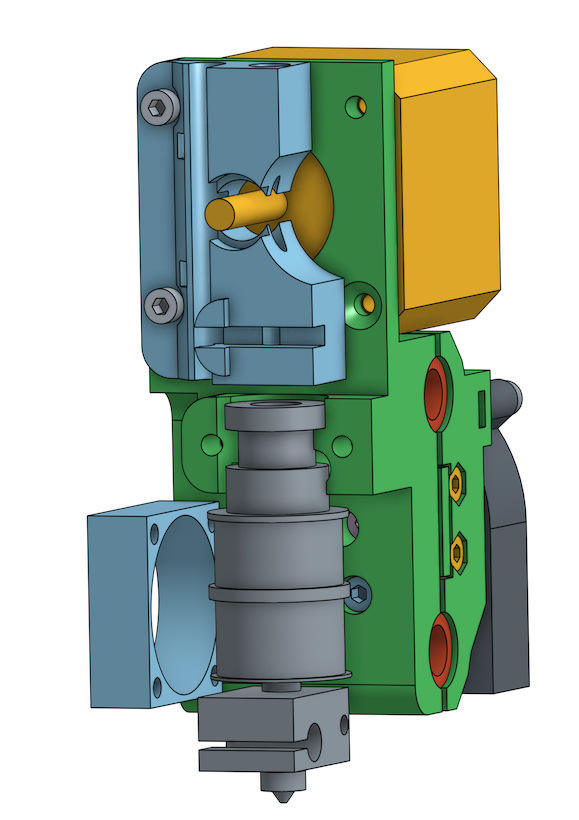
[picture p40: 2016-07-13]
images/assembly extruder plate no clamp.png

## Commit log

2016-07-13 Describe how to assemble the front half of the x-carriage and extruder.
2017-03-25 Add Readme, License, DXF, and STL files.
    [Blower Duct Mk3 - Blower Duct Mk3.stl, Lasercut Frame - Face-2.dxf, Lasercut Frame - Face-3.dxf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]
2017-03-25 Build manual small edits for newer X carriage fan mount switching from M4 nuts to M3
